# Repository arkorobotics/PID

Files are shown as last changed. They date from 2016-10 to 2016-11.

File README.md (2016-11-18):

# PID

This project is intended for teaching the general public about PID controllers and gain tuning methods.

In order to better understand PID, users are encouraged to build a simple electromechanical system consisting of a motor, a motor driver, an encoder, and a microcontroller. The system is then put out of balanced by mounting a metal bar at the end of the motors output shaft, making it difficult for the motor to maintain a constant position or velocity. 

This is where PID controllers come into play. Using the code provided in this repository, users can implement a PID controller in software, and easily tune the gain values of the controller to stabilize the system such that it maintains a desired position or velocity.

In this repository you will find the necessary hardware, software, and schematics to build this system.

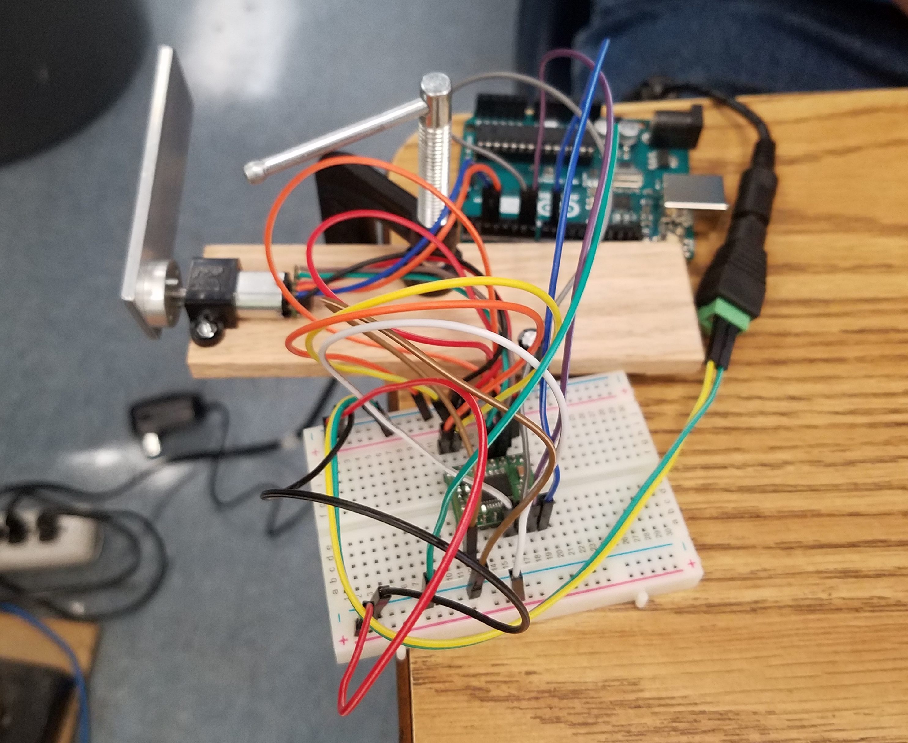
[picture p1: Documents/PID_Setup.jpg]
PID Setup


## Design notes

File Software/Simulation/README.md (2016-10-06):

# PID Simulator

In this iPython notebook, we explore PID controllers and gain tuning methods. 

We first start by modeling our system, then by applying PID controllers to compensate for error. Using the tuning methods provided in our documentation, students will learn how to tune the PID gain values to optimize for rise time, overshoot, settle time, steady-state error, and stability.

## Installation

You will need to install [iPython](http://ipython.org/) and few libraries:

```
pip3 install numpy
pip3 install scipy
pip3 install matplotlib

pip3 install control
```

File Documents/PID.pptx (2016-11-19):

## PID

Ara Kourchians

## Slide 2

Physical
World

Control

Desired
World

## Open Loop

Physical
World

Control

Desired
World

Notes: Simple autonomous mode that follows a script
Sprinkler system on a timer
Motor + battery
You “trust” that it works and assume ideal conditions

## Closed Loop

Physical
World

Control

Sensing

Desired
World

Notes: Air Conditioners
Airplanes auto-pilot
Drones

## ??? Loop

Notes: - Based on the previous definition, is this a closed or open loop system?

## Closed Loop

X

Sensing

## Closed Loop

X

Sensing

Control

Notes: - Explain how the students observe where the robot is and come up with a control command to give the robot, but this has a problem….

## Closed Loop

X

Sensing

Control

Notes: This requires training, learning, ‘piloting’
Robot might not drive perfectly straight
Might slip, or be going uphill and will require the driver to manually add more power
So far, the driver has had to learn each robot.. and every robot is different

## Some terminology

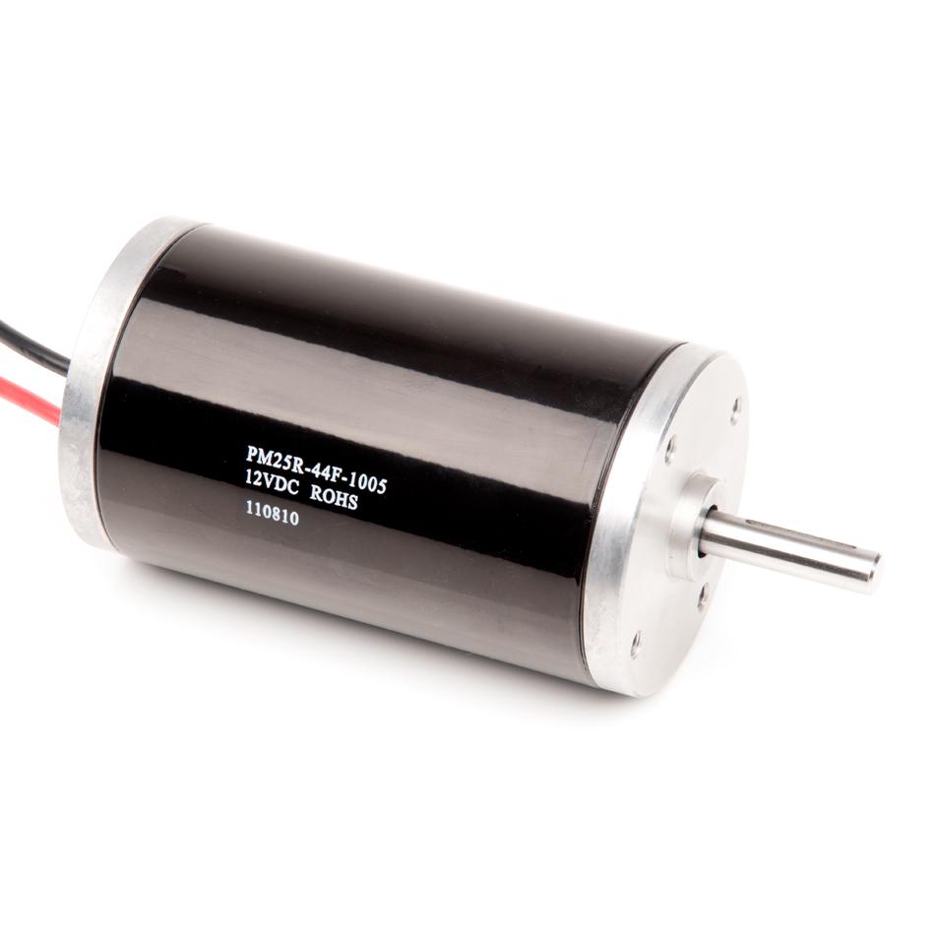
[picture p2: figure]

Motor

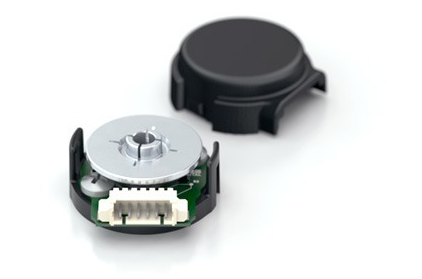
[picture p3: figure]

Encoder

State

Target

Error

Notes: The story is different for autonomous mode

## Autonomous Mode

X

State

Target

Error

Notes: The story is different for autonomous mode

## Autonomous Mode

autonomous.c

X

State

Target

Error

## Autonomous Mode

autonomous.c

void go()
{
robot.drive(X);
}

0

X

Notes: How do you actually write this in terms of motors and sensors?

## Autonomous Mode

autonomous.c

void go()
{
robot.motors(100);
wait(1_SEC);
robot.motors(0); ..
}

0

X

Error

X+Error

## Autonomous Mode

autonomous.c

void go()
{
robot.motors(100);
while(encoder < 1000)
{
encoder = robot.read();
}
robot.motors(0);
}

0

X

Error

X+Error

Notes: You’re going to overshoot when you get to your goal (100% to 0%)

## PID Control

0

Error

## PID Control

Proportional
Present
P*Error

Integral
Past
I*Sum_of_Errors

Derivative
Future
D*(Error- Last_Error)

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
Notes: PID controllers run in a loop, it’s iterative
Weights of each term depend on the system!
The P, I, and D terms are summed and used as the controller output

## Position Control Using PID

## Design

Gearbox

PID CONTROLLER

MOTOR

Wheel

ENCODER

## PID Block Diagram

P

I

D

Target

+

Σ

Error

+

+

+

Motor

Output

State

## PID Block Diagram

P

I

D

Target

+

Σ

Error

+

+

+

Motor

Output

State

Encoder

## Proportional Control

## Proportional Control

Motor = P * Error

0

Error

## Proportional Control

Motor = P * Error
100 = 2 * 50

0

Error

## Proportional Control

Motor = P * Error
20 = 2 * 10

0

Error

## Proportional Control

Motor = P * Error
1 = 2 * 1

0

Error

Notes: You may never reach it, or overshoot it
VERY system dependent ^
P term would be target distance dependent

## Proportional Control

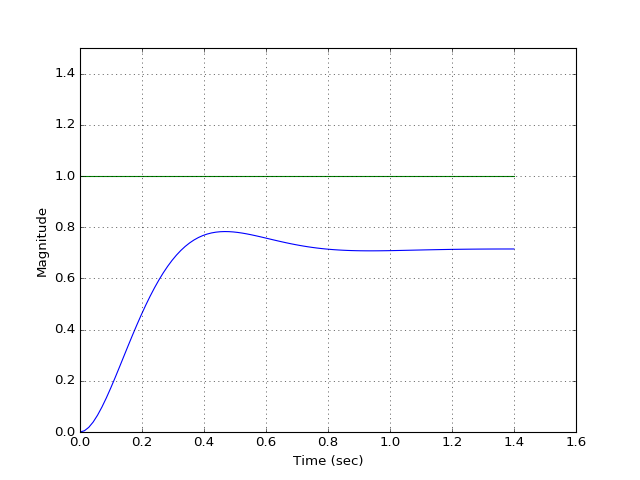
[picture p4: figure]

## Integral Control

## Integral Control

Error_Sum = Error_Sum + Error
50 = 0 + 50
95 = 50 + 45
115 = 95 + 20
115 = 115 + 0
75 = 115 + -40
25 = 75 + -50
-35 = 25 + -60
-85 = -35 + -50
Motor = I * Error_Sum
25 = 0.5 * 50
48 = 0.5 * 95
56 = 0.5 * 115
56 = 0.5 * 115
38 = 0.5 * 75
13 = 0.5 * 25
-17 = 0.5 * -35
-43 = 0.5 * -85

0

Error

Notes: You may never reach it, or overshoot it
VERY system dependent ^
P term would be target distance dependent

## Integral Control

Error_Sum = Error_Sum + Error
50 = 0 + 50
95 = 50 + 45
115 = 95 + 20
115 = 115 + 0
75 = 115 + -40
25 = 75 + -50
-35 = 25 + -60
-85 = -35 + -50
Motor = I * Error_Sum
25 = 0.5 * 50
48 = 0.5 * 95
56 = 0.5 * 115
56 = 0.5 * 115
38 = 0.5 * 75
13 = 0.5 * 25
-17 = 0.5 * -35
-43 = 0.5 * -85

0

Error

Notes: You may never reach it, or overshoot it
VERY system dependent ^
P term would be target distance dependent

## Integral Control

Error_Sum = Error_Sum + Error
50 = 0 + 50
95 = 50 + 45
115 = 95 + 20
115 = 115 + 0
75 = 115 + -40
25 = 75 + -50
-35 = 25 + -60
-85 = -35 + -50
Motor = I * Error_Sum
25 = 0.5 * 50
48 = 0.5 * 95
56 = 0.5 * 115
56 = 0.5 * 115
38 = 0.5 * 75
13 = 0.5 * 25
-17 = 0.5 * -35
-43 = 0.5 * -85

0

Error

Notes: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

## Integral Control

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

0

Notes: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

## Integral Control

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

0

-Error

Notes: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

## Integral Control

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

0

-Error

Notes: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

## Integral Control

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

0

-Error

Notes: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

## Integral Control

Error_Sum = Error_Sum + Error
50 = 0 + 50
95 = 50 + 45
115 = 95 + 20
115 = 115 + 0
75 = 115 + -40
25 = 75 + -50
-35 = 25 + -60
-75 = -35 + -40
Motor = I * Error_Sum
25 = 0.5 * 50
48 = 0.5 * 95
56 = 0.5 * 115
56 = 0.5 * 115
38 = 0.5 * 75
13 = 0.5 * 25
-17 = 0.5 * -35
-38 = 0.5 * -75

0

-Error

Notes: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

## Integral Control

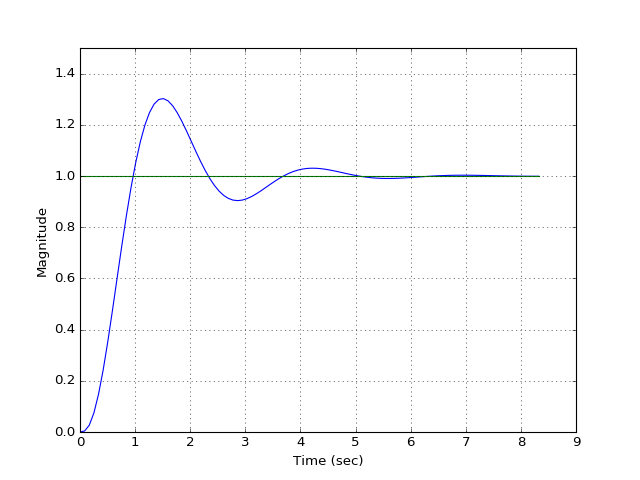
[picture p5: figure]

## Derivative Control

## Derivative Control

Motor = D* (Error – Last_Error)
25. = 0.5 * (50 – 0)

0

Error

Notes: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

## Derivative Control

Motor = D* (Error – Last_Error)
25 = 0.5 * (50 – 0)
-5 = 0.5 * (40 – 50)

0

Error

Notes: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

## Derivative Control

Motor = D* (Error – Last_Error)
25 = 0.5 * (50 – 0)
-5 = 0.5 * (40 – 50)
-2.5 = 0.5 * (35 – 40)

0

Error

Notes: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

## Derivative Control

Motor = D* (Error – Last_Error)
25 = 0.5 * (50 – 0)
-5 = 0.5 * (40 – 50)
-2.5 = 0.5 * (35 – 40)
0 = 0.5 * (35 – 35)

0

Error

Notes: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

## Derivative Control

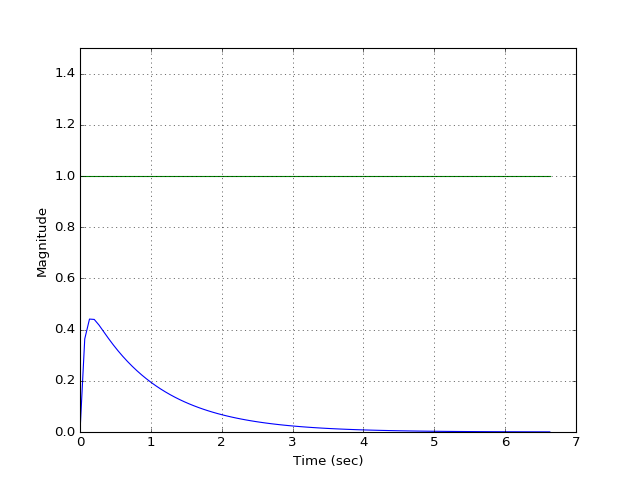
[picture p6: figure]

## PID Plot Terminology

## PID Plot Terminology

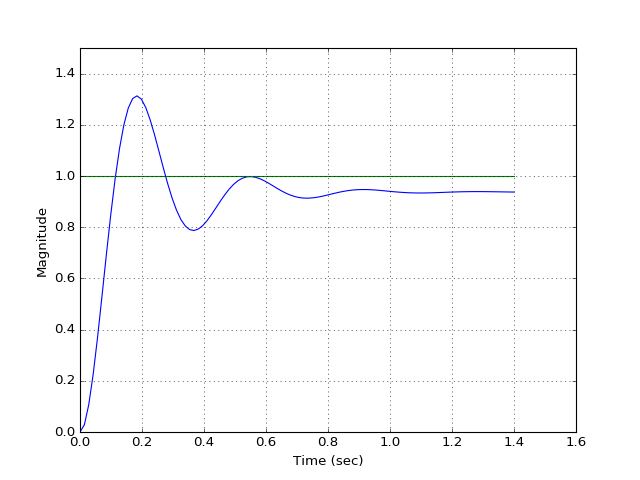
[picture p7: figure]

Overshoot

Steady-State Error

Rise Time

Settling Time

## P = 50

## P = 100

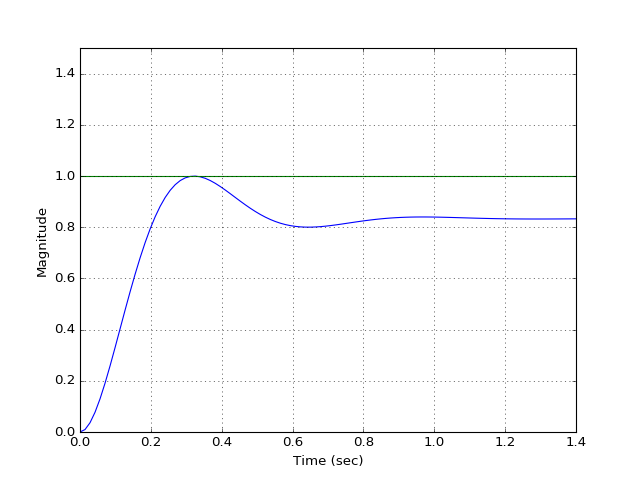
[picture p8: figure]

## P = 300

## I = 10

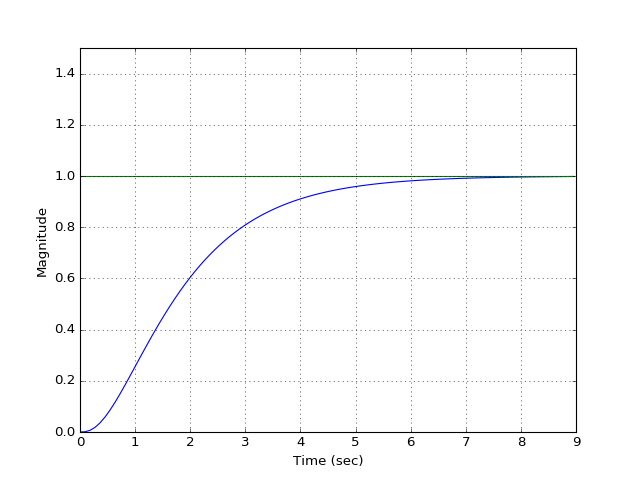
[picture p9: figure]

## I = 50

## I = 80

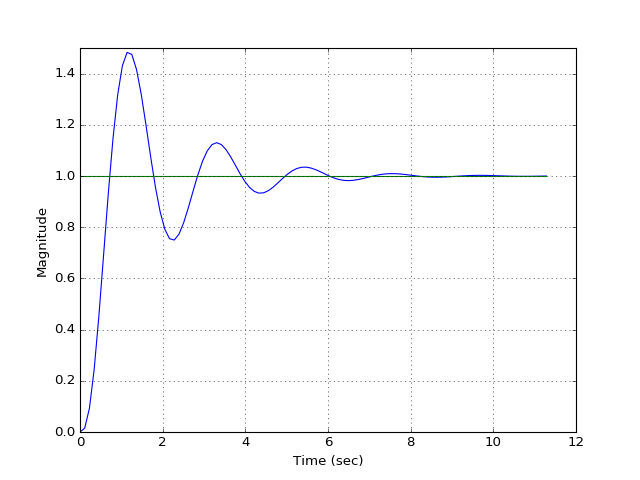
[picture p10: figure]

## D = 10

## D = 100

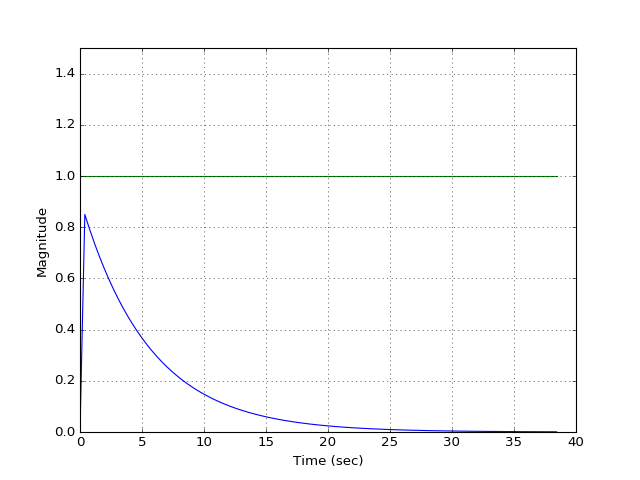
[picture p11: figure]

## PID Tuning Methods

## PID Plot Terminology

Overshoot

Steady-State Error

Rise Time

Settling Time

## PID Tuning Methods

Parameter Increase | Rise Time | Overshoot | Settling Time | Steady-State Error
Kp | | | Small Change
Ki
Kd | Small Change | | | Small Change

## P = 30, I = 0, D = 0

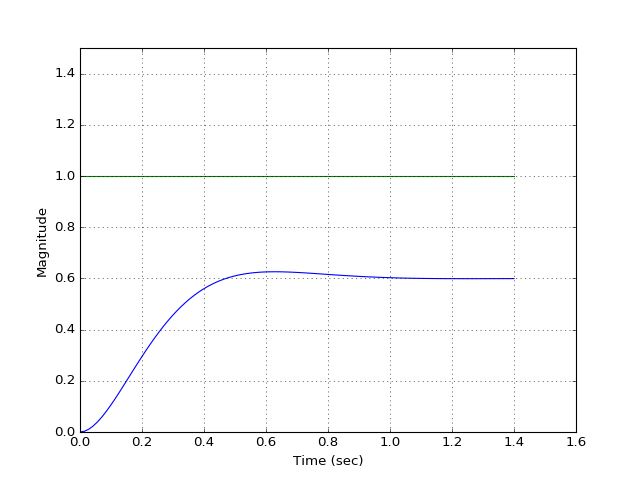
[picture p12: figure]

## P = 30, I = 15, D = 0

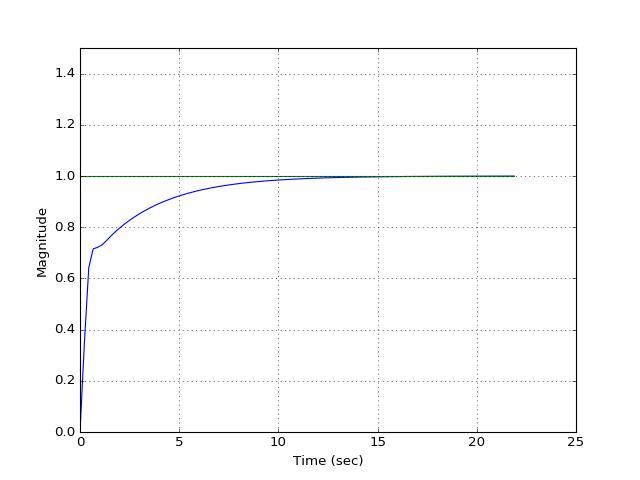
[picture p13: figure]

## P = 30, I = 30, D = 0

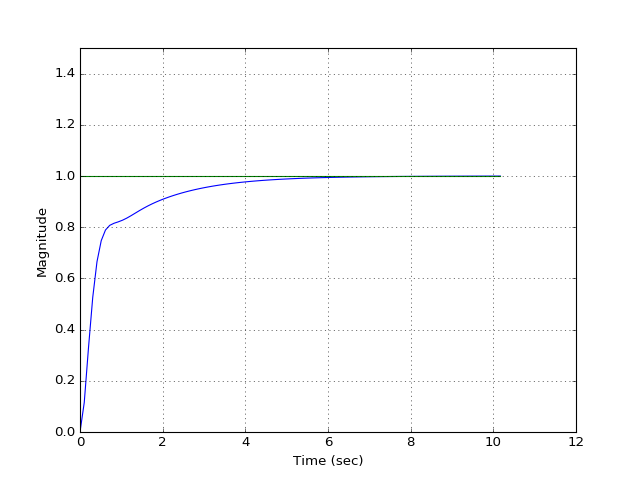
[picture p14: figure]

## P = 30, I = 60, D = 0

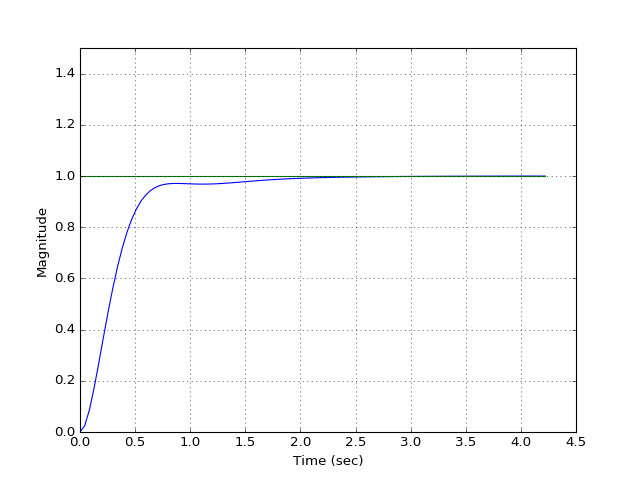
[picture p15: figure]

## P = 30, I = 80, D = 0

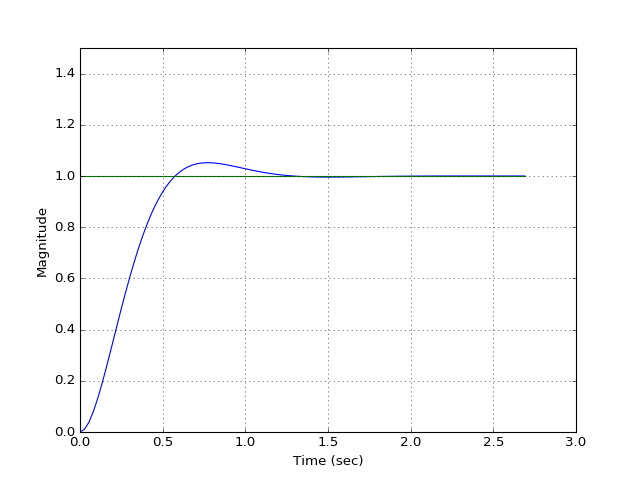
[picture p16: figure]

## P = 30, I = 70, D = 0

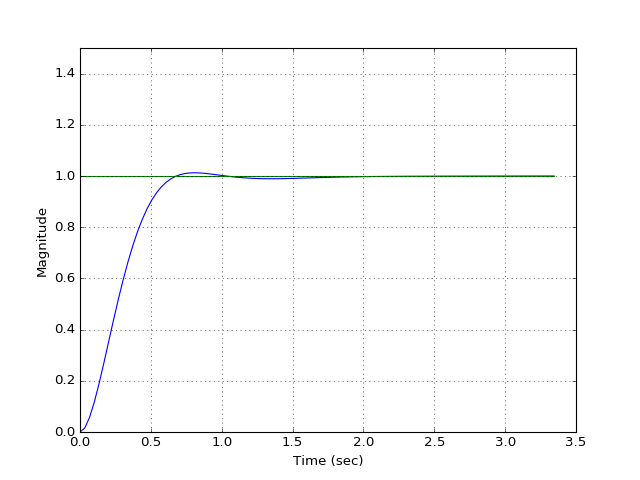
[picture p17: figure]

## P = 30, I = 70, D = 10

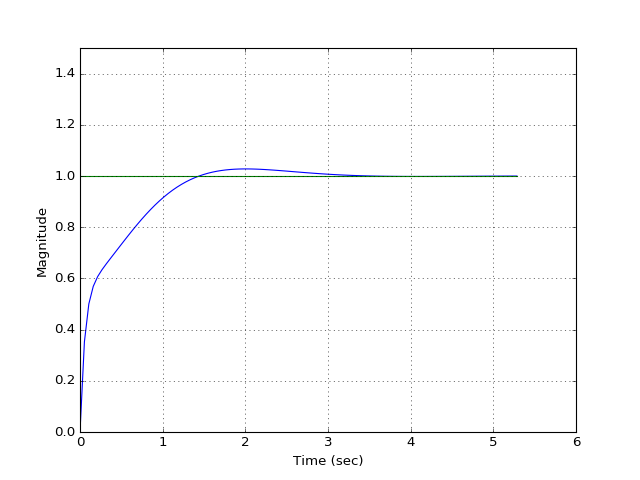
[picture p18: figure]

## P = 30, I = 70, D = 1

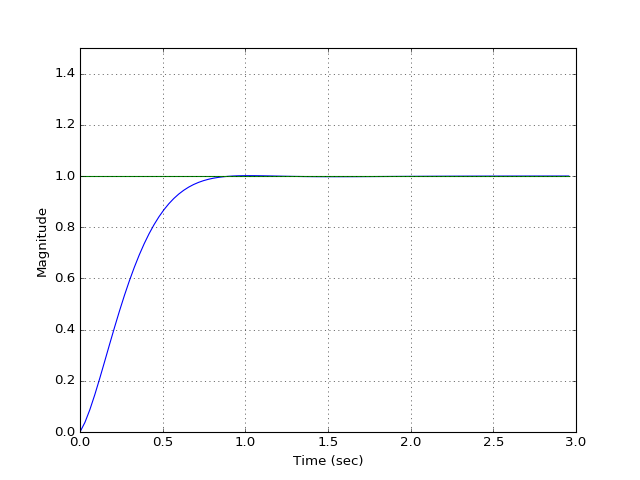
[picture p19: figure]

## “The Right Way” (beyond our scope)

## Model

Digital
Motor Speed
Or
Digital
Motor Position

Physical
Motor Speed
Or
Physical
Motor Position

+

Σ

Controller

Plant

## Model

Digital
Motor Speed
Or
Digital
Motor Position

Physical
Motor Speed
Or
Physical
Motor Position

+

Σ

Controller

Plant

## Model

Digital
Motor Speed
Or
Digital
Motor Position

Physical
Motor Speed
Or
Physical
Motor Position

+

Σ

Controller

Plant

PID Control Loop

Physical Motor & Wheel

## Model

Encoder

Digital
Motor Speed
Or
Digital
Motor Position

Physical
Motor Speed
Or
Physical
Motor Position

+

Σ

Controller

Plant

PID Control Loop

Physical Motor & Wheel

## Time and S Domain

- Mass:
- Damper:
- Spring:

M

M*s^2

D*s

K

## Physical Motor & Wheel

+
Ea

Gearbox

MOTOR

Wheel

θm

## Physical Motor & Wheel

Kt
Kb

Motor

+
Ea

Ra

Gearbox

Vemf

- +

La

Ja
Da

Wheel

θm

## Spec'ing Motors

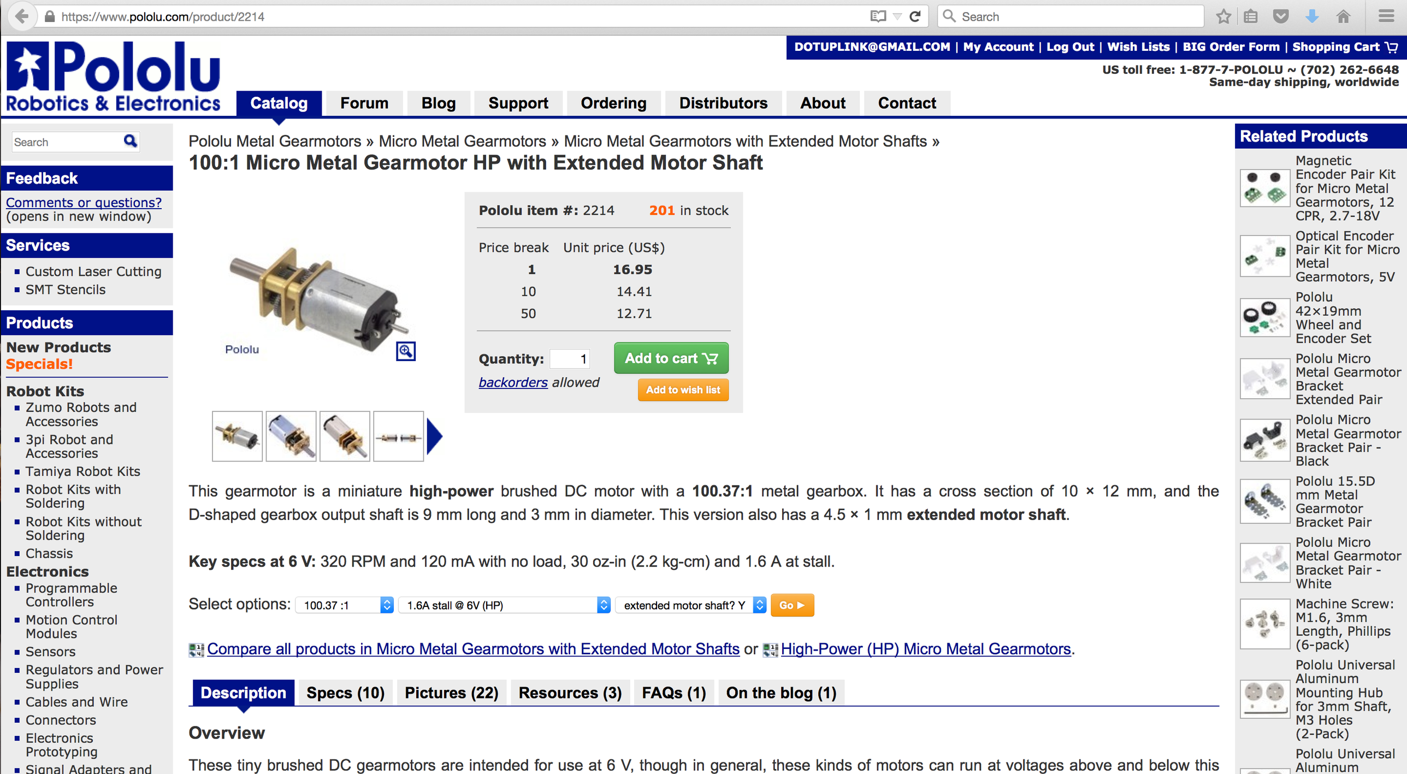
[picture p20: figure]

## Spec'ing Motors

τ (N-m)

No Load Speed: 320 RPM -> 33.51 rad/sec

Stall Torque: 30 oz-in -> 0.2118 N-m

0.2118 N-m
(1.6A)

ω (rad/sec)

33.51 rad/sec
(6V)

## Physical Motor & Wheel

Motor

+
Ea

Ra = 1Ω

La =
0.005H

Gearbox

Vemf

- +

θa

Wheel

Ja = 0
Da = 0

θm

## Physical Motor & Wheel

Motor

Gearbox

+
Ea

Ra = 1Ω

La =
0.005H

N1 = 1

Vemf

- +

Wheel

θm

N2 = 100

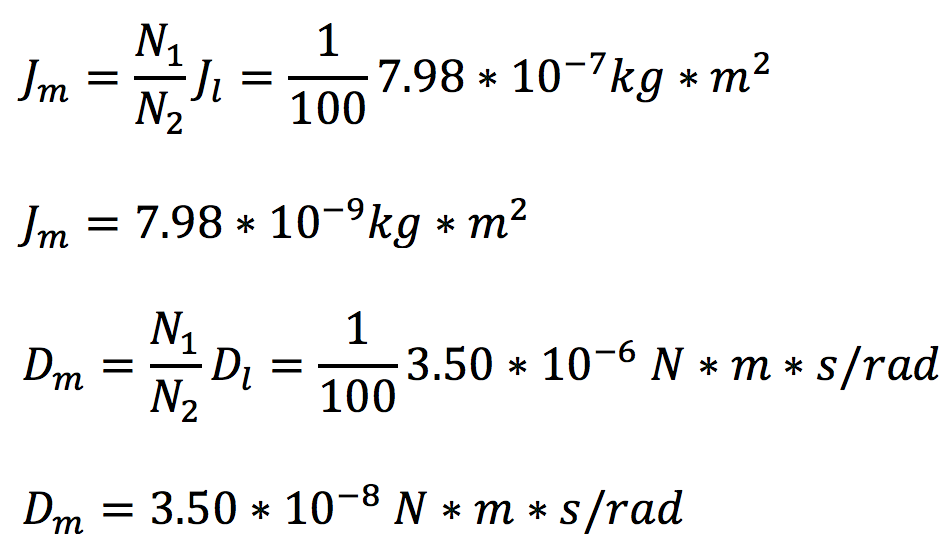
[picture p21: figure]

## Physical Motor & Wheel

Motor

Gearbox

+
Ea

Ra = 1Ω

La =
0.005H

N1 = 1

Vemf

- +

Wheel

θm

N2 = 100

## Physical Motor & Wheel

Motor

Gearbox

+
Ea

Wheel

- +

θm

## Design

Digital
Motor Speed
Or
Digital
Motor Position

Physical
Motor Speed
Or
Physical
Motor Position

+

Σ

Controller

## Controller

ACTION =

NOW

+

PAST

+

FUTURE

## Model

Digital
Motor Speed
Or
Digital
Motor Position

Physical
Motor Speed
Or
Physical
Motor Position

+

Σ

1

## Controller

Kp

Ki

Kd

## DEMO!

## Hardware

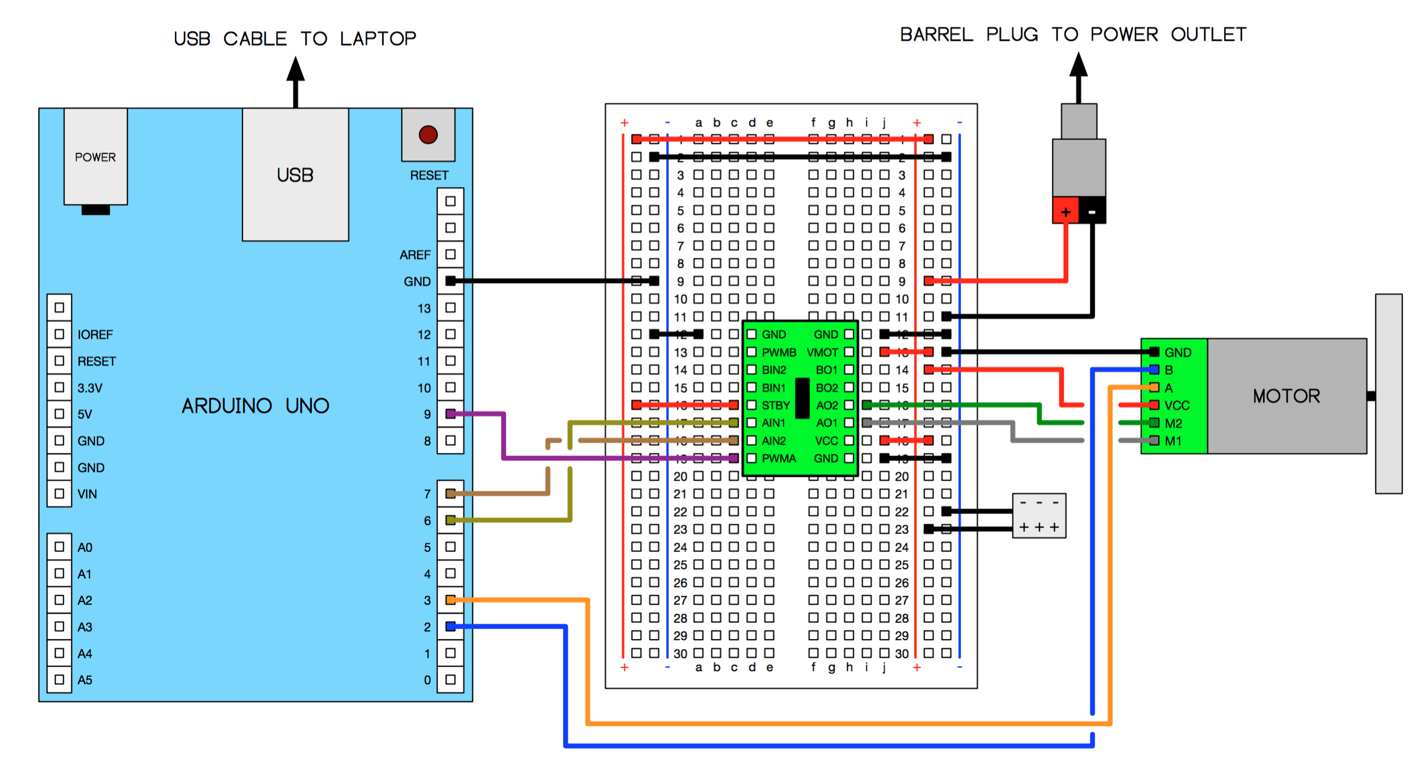
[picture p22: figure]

## Common Mistakes

- PID loop in non timer based interrupt

void loop()
{ // Update the angle using the gyro as often as possible.
updateAngleGyro(); // Every 20 ms (50 Hz), correct the angle using the
// accelerometer, print it, and set the motor speeds.
static byte lastCorrectionTime = 0;
byte m = millis();
if ((byte)(m - lastCorrectionTime) >= 20)
{
lastCorrectionTime = m;
correctAngleAccel();
printAngles();
setMotors(); // PID Loop
}
}

## Common Mistakes

- PID loop in non timer based interrupt
  - Why is this such a bad thing to do?
    - Holding up the system kills the PID controller
    - Variation in execution time means changing dt in integration and derivative terms
  - What does this mean?
    - No longer meeting timing/control authority constraints
    - Possibly unstable system

## Common Mistakes

- Not recording & plotting e(t) and c(t) during the tuning process
    - You’re left to visually observe systems response
    - There maybe more going on than what’s visible
    - Time wasted trying different gain values without quantitatively knowing how it effects the response time
- Not recording & plotting the P, I, D terms individually
    - Not knowing how each term is contributing to c(t)
    - Hard to work back where noise/problems are coming from

## Common Mistakes

- Not methodically tuning
  - Doing random P, I, D term tuning can be a HUGE time sink
  - Solution?
    - Follow a method
    - Understand the response
    - Make educated changes to your gain values
- Not knowing which terms you need
  - PID? PI? PD?
  - I.E. – using D term on a noisy accelerometer

## Common Mistakes

- Not normalizing/mapping
  - P = 2432, I = 1693, D = 303… wat
  - Normalize/Unity Gain: 0.0 – 1.0 (assuming FPU)
- Using floating point variables
  - Dangerous to do floating point math on embedded systems without FPU

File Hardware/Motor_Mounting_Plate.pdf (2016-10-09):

6 | 5 | 4 | 3 | 2 | 1

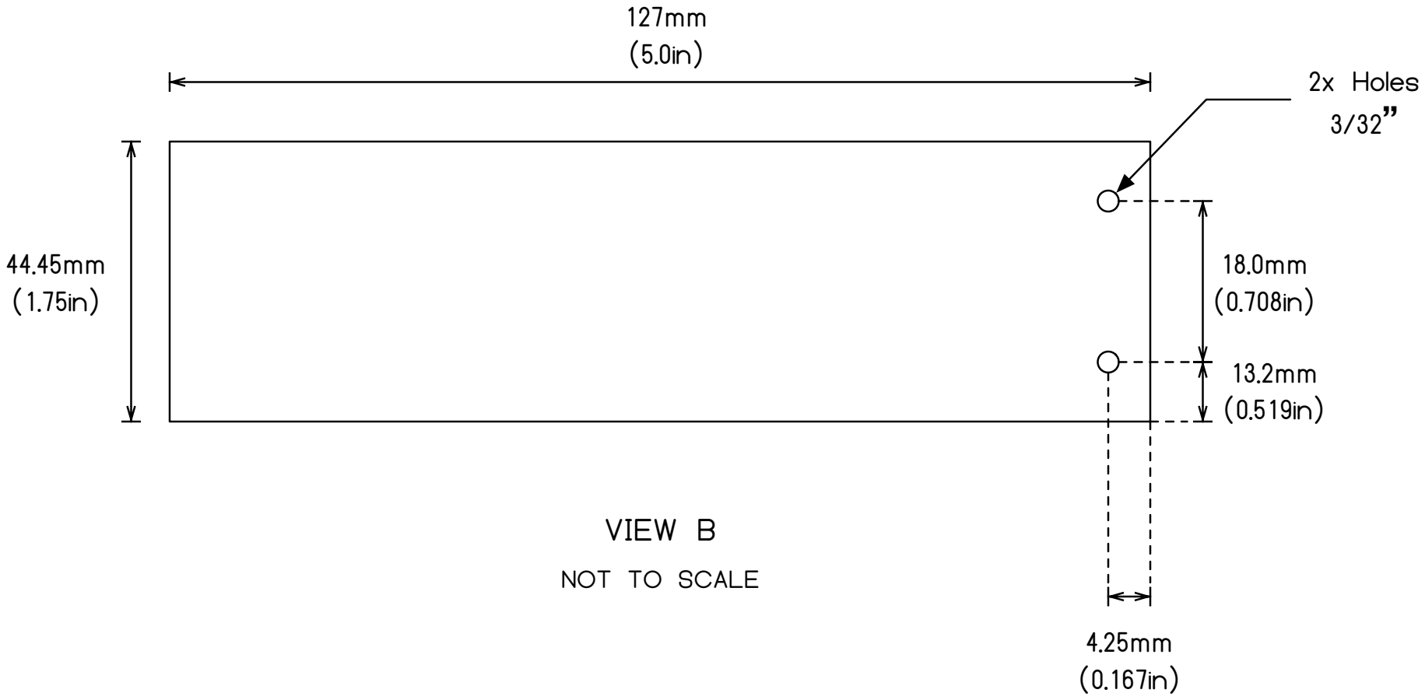
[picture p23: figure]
VIEW B; NOT TO SCALE; 2x Holes 3/32”
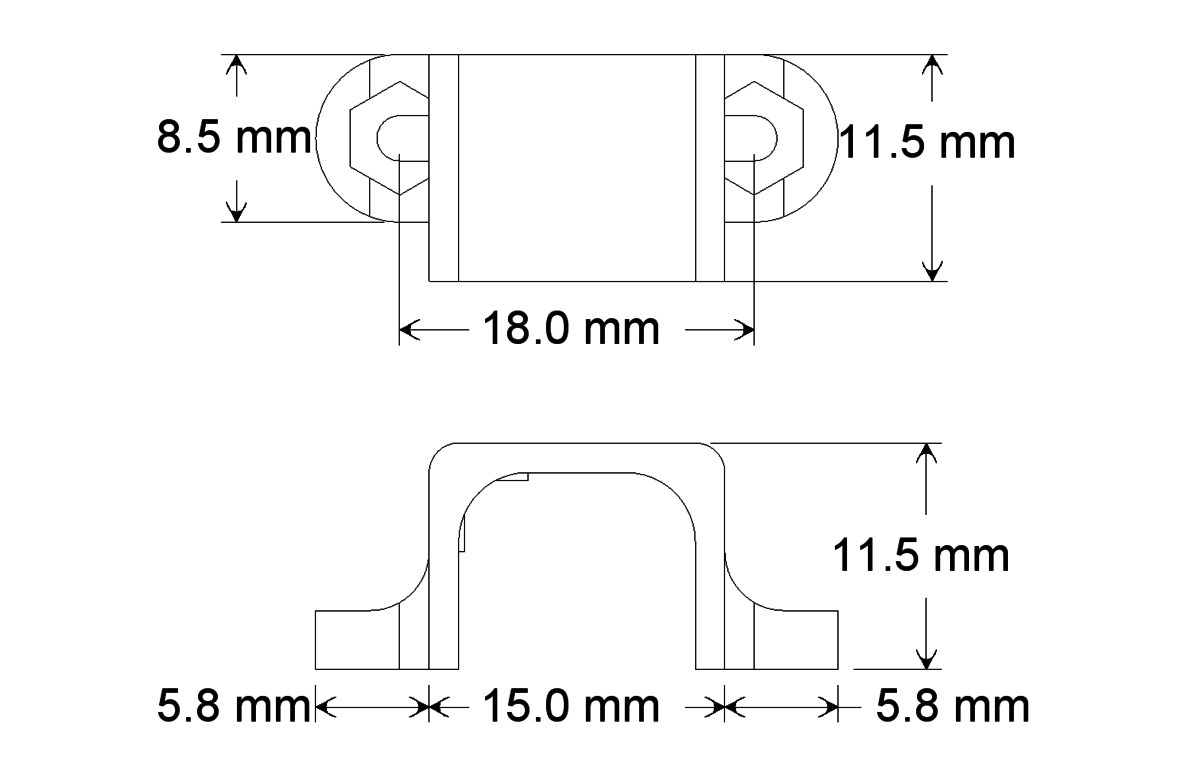
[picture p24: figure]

6 | 5 | 4 | 3 | 2 | 1

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
MOTOR MOUNTING PLATE
CRESCENTA VALLEY HIGH SCHOOL ROBOTICS TEAM 589

MM
(IN)

VIEW B: PLATE

VIEW A: BRACKET

VIEW A

6.35mm (0.25in) Thick
Wood or Lexan

44.45mm
(1.75in)

6.35mm
(0.25in)

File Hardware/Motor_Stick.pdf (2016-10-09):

6 | 5 | 4 | 3 | 2 | 1

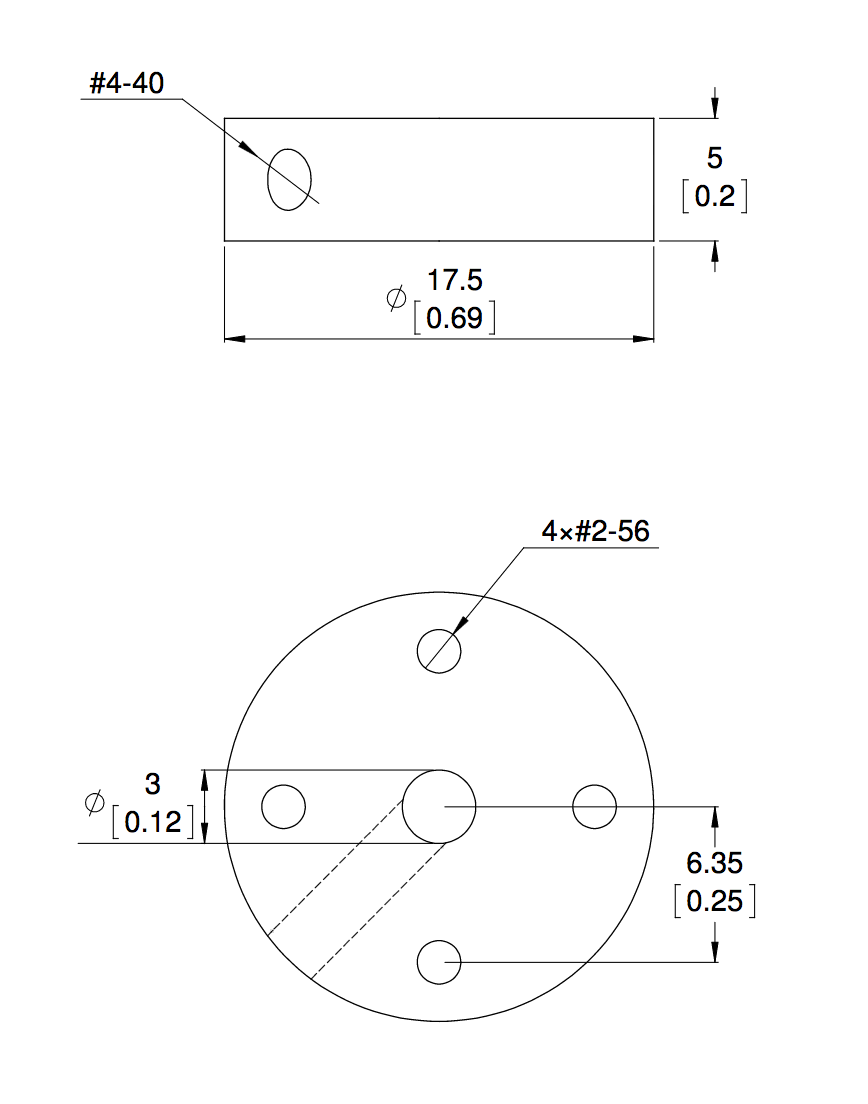
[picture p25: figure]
2x Holes 3/32”; 8mm (0.314in) VIEW A VIEW B

6 | 5 | 4 | 3 | 2 | 1

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
MOTOR STICK
CRESCENTA VALLEY HIGH SCHOOL ROBOTICS TEAM 589

MM
(IN)

VIEW B: STICK

VIEW A: HUB

NOT TO SCALE

3.175mm
(0.125in)

25.4mm
(1.0in)
25.4mm(1.0in) Thick
Wood, Aluminum or Lexan

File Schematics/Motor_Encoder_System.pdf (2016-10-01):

6 | 5 | 4 | 3 | 2 | 1

ARDUINO UNO; GND; AREF; VIN; RESET; IOREF; POWER; MOTOR; GND B A VCC M2 M1; VCC; VMOT; PWMA; AIN2; AIN1; STBY; BIN1; BIN2; PWMB; USB

6 | 5 | 4 | 3 | 2 | 1

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
## MOTOR ENCODER SYSTEM

## CRESCENTA VALLEY HIGH SCHOOL ROBOTICS TEAM 589

USB CABLE TO LAPTOP | BARREL PLUG TO POWER OUTLET

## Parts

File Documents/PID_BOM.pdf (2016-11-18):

## PID BOM

Qty | Part | Price | Link
1 Pololu Universal Aluminum Mounting Hub for 3mm Shaft, #2-56 Holes (2-Pack) | | 5.95 https://www.pololu.com/product/1079
1 Pololu Micro Metal Gearmotor Bracket Pair - Black | | 4.99 https://www.pololu.com/product/989
1 TB6612FNG Dual Motor Driver Carrier | | 4.95 https://www.pololu.com/product/713
1 Arduino Uno R3 | | 24.95 https://www.pololu.com/product/2191
1 Wall Power Adapter: 5VDC, 3A, 5.5×2.1mm Barrel Jack, Center-Positive | | 9.95 https://www.pololu.com/product/1461
1 Magnetic Encoder Pair Kit for Micro Metal Gearmotors, 12 CPR, 2.7-18V (HPCB compatible) | | 8.95 https://www.pololu.com/product/3081
1 0.100" (2.54 mm) Breakaway Male Header: 2×40-Pin, Straight | | 1.49 https://www.pololu.com/product/966
1 400-Point Breadboard | | 3.75 https://www.pololu.com/product/351
1 150:1 Micro Metal Gearmotor MP 6V with Extended Motor Shaft | | 16.95 https://www.pololu.com/product/2382
1 Machine Screw: #2-56, 7/16" Length, Phillips (25-pack) | | 0.99 https://www.pololu.com/product/1957
1 Honbay® 120pcs Multicolored Jumper Wires Ribbon Cables Kit | | 7.97 https://www.amazon.com/Honbay%C2%AE-120pcs-Multicolored-Female-Breadboard/dp/B017NEGTXC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
1 AmazonBasics USB 2.0 Cable - A-Male to B-Male - 6 Feet (1.8 Meters) | | 4.99 https://www.amazon.com/AmazonBasics-USB-2-0-Cable--Male/dp/B00NH11KIK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
1 | Grizzly H0481 Aluminum C-Clamps, Set of 6, 1-Inch Opening | 13.29 https://www.amazon.com/Grizzly-H0481-Aluminum-C-Clamps-Opening/dp/B0000DD147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
1 5 x Female 2.1x5.5mm DC Power Cable Jack Adapter Connector | | 5.09 https://www.amazon.com/IKADEER-Female-2-1x5-5mm-Adapter-Connector/dp/B01KMBPJUM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
1 Motor Mounting Plate (Wood or Lexan) | https://github.com/arkorobotics/PID/blob/master/Hardware/Motor_Mounting_Plate.dxf
1 Motor Stick (Wood, Metal, or Lexan) | https://github.com/arkorobotics/PID/blob/master/Hardware/Motor_Stick.dxf
TOTAL | 114.26

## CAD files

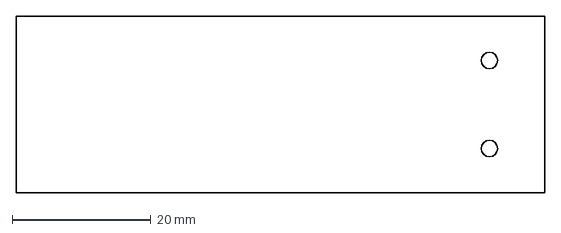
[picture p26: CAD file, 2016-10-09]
Hardware/Motor_Stick.dxf
76.2 x 25.4 mm

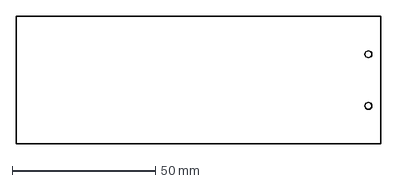
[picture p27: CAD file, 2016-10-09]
Hardware/Motor_Mounting_Plate.dxf
127.0 x 44.5 mm

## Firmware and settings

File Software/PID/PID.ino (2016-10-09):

// Simple PID Controller
// By: Ara Kourchians
// ----------------------------------------------------------------------------

// LED Variables
const byte ledPin = 13;

// Encoder Variables
#define TICK_NULL 0
#define TICK_A 1
#define TICK_B 2
#define FORWARD 0
#define BACKWARD 1
const byte encoder_A_pin = 3;
const byte encoder_B_pin = 2;
volatile static unsigned char last_tick_a = TICK_NULL;
volatile static unsigned char last_tick_b = TICK_NULL;
volatile long position_ticks = 0;
volatile unsigned long current_time = 0;
volatile unsigned long last_time = 0;

// State Variables
volatile static unsigned char cmd_direction = FORWARD;
volatile float position = 0.0; // degrees
volatile float velocity = 0.0; // rpm

// PID Variables
volatile const float target = 90.0; 
volatile float P_gain = 0.01;
volatile float I_gain = 0.001;
volatile float D_gain = 0.00;
volatile float error = 0;
volatile float last_error = 0;
volatile float sum_of_error = 0;
volatile float pid_output = 0;

// Motor Variables
const byte AI0_pin = 6;
const byte AI1_pin = 7; 
const byte motor_pin = 9;
volatile static unsigned char motor_output = 0;
volatile static unsigned char read_direction = FORWARD;

// Runs first and once
void setup() 
{
  pinMode(ledPin, OUTPUT);
  
  // Setup encoder interrupt routines
  last_tick_a = digitalRead(encoder_A_pin) ? 1 : 0;
  last_tick_b = digitalRead(encoder_B_pin) ? 1 : 0;

  pinMode(encoder_A_pin, INPUT_PULLUP);
  attachInterrupt(digitalPinToInterrupt(encoder_A_pin), encoderTickA, CHANGE);

  pinMode(encoder_B_pin, INPUT_PULLUP);
  attachInterrupt(digitalPinToInterrupt(encoder_B_pin), encoderTickB, CHANGE);

  // Set Motor Direction
  setDirection(FORWARD);

  // Set Motor Speed to Zero
  analogWrite(motor_pin, motor_output);
  
  // Initialize Serial Bus
  Serial.begin(115200);
}

// Main Loop
void loop() 
{
  digitalWrite(ledPin, read_direction);
  
  // Update Position and Velocity
  position = ((float)position_ticks)*(360/1800.0);
  velocity = (0.000555)/(0.000001*((float)(current_time - last_time + 1)));

  // PID Calculations
  last_error = error;           // Store the last error for derivative term
  error = target - position;    // Calculate new error
  sum_of_error = sum_of_error + error;    // Accumulate error for integral term
  if(sum_of_error > 1000)                 // Saturate to prevent large integral term
  {
    sum_of_error = 1000;
  }
  
  // PID Controller
  pid_output = P_gain*error + I_gain*sum_of_error + D_gain*(error - last_error);

  // Hard limit PID output
  if(pid_output > 1.0)                                   
  {
    pid_output = 1.0;
  }
  if(pid_output < -1.0)
  {
    pid_output = -1.0;
  }

  if(pid_output >= 0.0 && cmd_direction == BACKWARD)     // Set direction
  {
    setDirection(FORWARD);
  }
  if(pid_output < 0.0 && cmd_direction == FORWARD)
  {
    setDirection(BACKWARD);
  }
  
  motor_output = (unsigned char)(254.0*abs(pid_output)); // Calculate
  analogWrite(motor_pin, motor_output);                  // Apply output to motor 
  
  // Print out data for plotting
  Serial.print(target);
  Serial.print(" ");
  Serial.println(error);
  
  delay(50);  // 20Hz Update Rate
              // Do not change this time delay. Changing this time delay
              // will effect the controller and the response of the system, given
              // a set of PID gain values. 
              //
              // TODO: This loop should actually be in a timer interrupt
              // with a fixed/non-maskable update rate. 
}

void setDirection(unsigned char input_direction)
{
  // Set Motor Direction
  cmd_direction = input_direction ? 1 : 0;
  digitalWrite(AI0_pin, (~cmd_direction & 0x01));
  digitalWrite(AI1_pin, cmd_direction);
}

void encoderTickA() 
{
  unsigned char tick_a = digitalRead(encoder_A_pin) ? 1 : 0;
  unsigned char tick_b = digitalRead(encoder_B_pin) ? 1 : 0;

  // XOR ticks to find direction
  unsigned char plus = tick_a ^ last_tick_b;
  unsigned char minus = tick_b ^ last_tick_a;

  if(plus) 
  {
    position_ticks++;
    read_direction = FORWARD;    
  }
  if(minus) 
  {
    position_ticks--;
    read_direction = BACKWARD;
  }

  last_tick_a = tick_a;
  last_tick_b = tick_b;

  last_time = current_time;
  current_time = micros();
}

void encoderTickB() 
{
  unsigned char tick_a = digitalRead(encoder_A_pin) ? 1 : 0;
  unsigned char tick_b = digitalRead(encoder_B_pin) ? 1 : 0;

  // XOR ticks to find direction
  unsigned char plus = tick_a ^ last_tick_b;
  unsigned char minus = tick_b ^ last_tick_a;

  if(plus) 
  {
    position_ticks++;
    read_direction = FORWARD;    
  }
  if(minus) 
  {
    position_ticks--;
    read_direction = BACKWARD;
  }

  last_tick_a = tick_a;
  last_tick_b = tick_b;

  last_time = current_time;
  current_time = micros();
}

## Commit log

2016-09-24 Added PID code
2016-09-27 fixed encoder, pid position control working
    [PID.ino]
2016-09-30 Added schematics and hardware, moved motor and encoder pins
    Added schematics and hardware, moved motor and encoder pins
2016-10-01 Updated schematic and hardware
    Updated schematic and hardware
2016-10-01 Added python notebook and power point slides
    Added python notebook and power point slides
2016-10-03 Simple second order system and PID added
    Simple second order system and PID added
2016-10-05 Added PID tuning methods, plot characteristics, and updated simulation notebook to reflect slides.
2016-10-07 Added PID Block Diagram
2016-10-09 Added comments to code and fixed missing D-term calc
    [PID.ino]
2016-10-09 Added a PDF version of the PID Power Point
2016-10-09 Added BOM and DXF files for hardware
    [Motor_Mounting_Plate.dxf, Motor_Stick.dxf, PID_BOM.xlsx]
2016-10-09 Added C Clamp to BOM
    [PID_BOM.xlsx]
2016-11-18 Updated BOM
    Updated BOM
    [PID_BOM.xlsx]
